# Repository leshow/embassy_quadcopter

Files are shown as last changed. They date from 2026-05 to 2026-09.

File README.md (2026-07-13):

# mini quadcopter in Rust w/ embassy for esp32 (WIP)

currently still a work in progress, building a (very) mini quadcopter for esp32 on bare metal with [embassy.dev](https://embassy.dev). right now using the esp32-c3 supermini, I may upgrade this to the s3 if the extra core is necessary.

## Quad assets

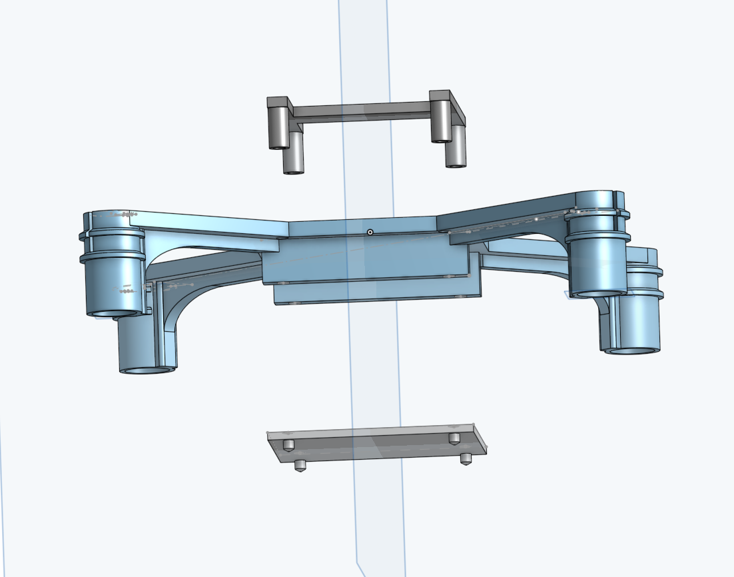
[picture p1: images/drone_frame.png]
drone frame


The frame stl & 3mf files are in the `stl/` dir and can be used to 3d print the frame. I created them in OnShape. For the battery compartment, I opted for a friction fit with pegs that you can also glue in. This got around some issues with printing supports that were a pain to remove.

There's a top stand that serves as a mount for the microcontroller and MPU6050 or ICM20948. I'll include a full parts list as the project progresses.

I've also created a prop guard you can mount as a single piece or in two halves, see the 3mf file in `stl/`

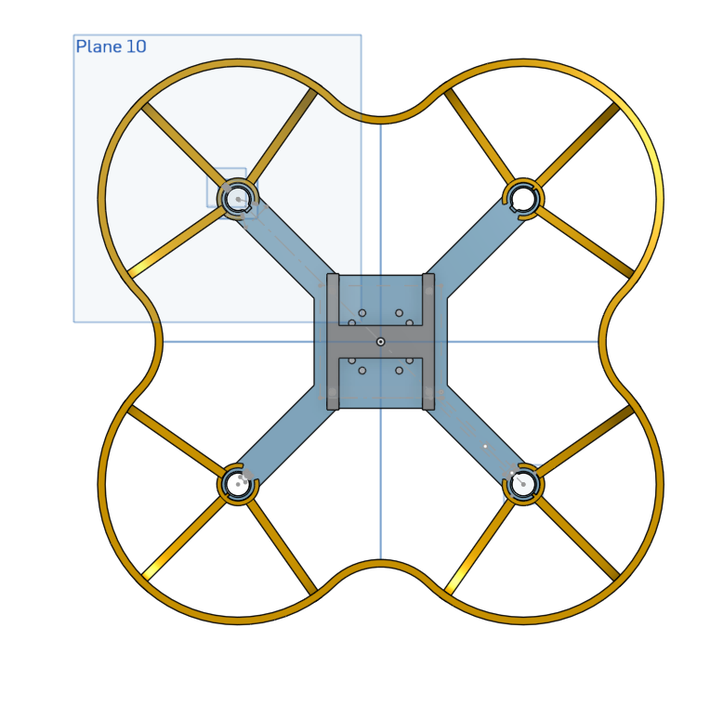
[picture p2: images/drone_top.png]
prop guard


They have a C-snap fit to the motor holders that should lock them into place pretty well. I've printed with a 0.4 and 0.6 nozzle on a bambu a1 and both results are usable. Obviously if you want cleaner layer lines go for the smaller nozzle.

I've printed in PLA, PETG and PETG-CF & GF. PLA seems totally fine, the drone frame is around 16 grams. The props are heavy at an additional 16 grams. They might require a bit of re-design but for indoor testing not so bad.

## Parts list

### Microcontrollers (choose one)

Currently only building on the c3 and c6. I'll try the s3 if I have time to attempt a build on the xtensa cores but RISC-V is better supported by embassy & Rust. The s3 supermini might be interesting because it's dual-core and has the same footprint as the c3.

| Part | Chip | Cores | Flash  | RAM | WiFi | Notes |
| --- | --- | --- | --- | --- | --- | --- |
| ESP32-C3 SuperMini | ESP32-C3 | 1× RV32 | 4 MB | 400 KB | 2.4 GHz | **Current build** - `c3` feature |
| ESP32-C6 SuperMini | ESP32-C6 | 1× RV32 | 4 MB | 512 KB | 2.4/5 GHz | Drop-in upgrade - `c6` feature |
| ESP32-S3 (16R8) | ESP32-S3 | 2× LX7  | 16 MB  | 8 MB PSRAM | 2.4 GHz | Dual-core; needs Xtensa toolchain - see `docs/s3-migration.md` |
| ESP32-S3 Mini | ESP32-S3 | 2× LX7  | 4/8 MB | - / 2 MB | 2.4 GHz | Compact form factor |

### IMU Sensors (choose)

| Part | DOF  | Interface | Accel | Gyro | Mag | Notes |
| --- | ---- | --- | ----- | ---- | --- | --- |
| ICM-20948 | 9DOF | I²C / SPI | ✓ | ✓ | ✓ AK09916 | **Current build** - yaw via magnetometer |
| MPU-6050  | 6DOF | I²C | ✓ | ✓ | ✗ | No yaw reference; cheaper and common |

### Other Components

| Part | Qty | Notes |
| --- | --- | --- |
| 8520 brushed motor | 4 | find it on aliexpress like everything else |
| mosfet 100N03A | 4 | One per motor |
| 1S LiPo battery (3.7v) | 1 | 3.7v 1s battery 25C or more discharge rate\*  |
| Propeller | 4 | 55 or 65mm |
| 3D printed frame | 1 | STL/3MF files in `stl/` - designed in OnShape |

Requires [espflash](https://github.com/esp-rs/espflash) for flashing (`cargo install espflash`).

\*I tried with a 503040 3.7v lipo recycled from a keyboard build but the BMS (battery management system) on it will automatically shut off after a few seconds. It's not really build to power these motors.

### ESP32-C3 (default)

```sh
cargo build -p embassy_quad --target riscv32imc-unknown-none-elf
cargo run -p embassy_quad --target riscv32imc-unknown-none-elf
```

Or using the aliases:

```sh
cargo build-c3
cargo flash-c3
```

### ESP32-C6

The C6 uses a different RISC-V target (`riscv32imac` vs `riscv32imc`). The
`c3` and `c6` features are mutually exclusive — always use
`--no-default-features` when building for C6 to avoid activating both:

```sh
cargo build-c6
cargo flash-c6
```

See .cargo/config.toml to see expansion of aliases

### Log level

`DEFMT_LOG` is read at compile time by `esp-println`:

```sh
DEFMT_LOG=debug cargo flash-c3
```

### Throttle cap

`THROTTLE_CAP` sets the max throttle at compile time, it will map your throttle input from 0-100 over the range you specify. For example, if you set `THROTTLE_CAP=50` and push the throttle to 80% it will translate into `.8 * 50 = 40%`.

## Visualizer

to see a 3d rendering of the orientation run:

```bash
DEFMT_LOG="info" LOG_RATE_MS=1 cargo flash-c3 --features visualize | (cd visualizer && cargo run)
```

It feeds the esp32 log output to a binary reading stdin and rendering a cube on screen

By default, sensor readings from the ICM-20948 are sent to the ESP32-C3 where either a Madgwick filter fuses accel and gyro data in software to correct orientation or the IMU's DMP is used to get the already fused output (`dmp` feature is on by default). The ICM-20948 also has an onboard DMP that fuses data directly on the sensor board. Output looks pretty good and doesn't have the yaw drift that the software fusion does when the magnetometer is enabled.

```sh
DEFMT_LOG="info" LOG_RATE_MS=1 cargo flash-c3 --features visualize | (cd visualizer && cargo run)
```

## Ground control

The `ground_control/` crate is a PC-side sender that reads a gamepad and streams control packets to the drone over UDP.

The drone runs a wifi AP (`esp-quad`, WPA2) with a static IP of `192.168.4.1`. There is no DHCP server, so you must assign yourself a static IP when connecting. The trick is to do this in a single `nmcli con add` — adding security and static IP separately doesn't work reliably:

```sh
nmcli con add type wifi con-name esp-quad ssid esp-quad \
  wifi-sec.key-mgmt wpa-psk \
  wifi-sec.psk <same as AP_PASSWORD> \
  ipv4.method manual \
  ipv4.addresses "192.168.4.2/24" \
  ipv4.gateway "192.168.4.1"
```

The AP password is set at build time via the `AP_PASSWORD` environment variable. If unset, the AP is open (remove the `wifi-sec.*` lines above).

Once the profile exists, connecting is just:

```sh
nmcli dev wifi rescan
nmcli con up esp-quad
```

Then run the ground control sender:

```sh
cd ground_control && RUST_LOG="info" cargo run --release
```

The left stick Y axis controls throttle (center = 0%, full up = 100%), left stick X controls yaw, and the right stick controls pitch/roll. The Start button toggles arm. Motors only spin when armed and throttle is above 0.

The drone IP and port can be overridden at build time:

```sh
RUST_LOG="info" GATEWAY_IP=192.168.4.1 UDP_PORT=4444 cargo run --release
```

## Testing

Unit tests live in `libs`, the crate shared between `firmware` and `ground_control` that defines the control/telemetry packet wire formats. It's the only crate that can build for the host, `firmware` can't (esp-hal's build script refuses to build for a non-embedded target), so there's nothing to run tests against there yet.

`telemetry` and `telemetry-verbose` each change the telemetry packet's wire format, so they're tested separately:

```sh
cargo test -p libs
cargo test -p libs --features telemetry
cargo test -p libs --features telemetry-verbose
```

## Docs

Check the `docs/` directory for some more info on assembly, setting up different controllers, sensors, etc.

## LLM usage

Docs and tests are sometimes generated with the use of LLMs, along with explanation/discovery, but the purpose of this project is to actually learn, so the code is still written by a human (hi!)

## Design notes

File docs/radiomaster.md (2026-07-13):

# RadioMaster Pocket as USB Gamepad for ground_control

How to configure a RadioMaster Pocket (EdgeTX) to act as a drop-in USB HID gamepad for `ground_control`, so the stick layout matches a regular Xbox-style controller with no code changes.

## Why this isn't plug and play

`ground_control` reads input through [gilrs](https://gitlab.com/gilrs-project/gilrs), which recognizes controllers by matching an SDL-style mapping database (Xbox controllers, PlayStation controllers, etc. are all in there). EdgeTX radios in USB joystick mode present a generic, fully configurable HID device under EdgeTX's own vendor ID, which is in nobody's mapping database.

Without a database entry, gilrs's Linux backend falls back to a fixed positional mapping based on the raw evdev axis/button codes (`native_ev_codes`):

| evdev code | gilrs axis/button |
| --- | --- |
| `ABS_X` | `Axis::LeftStickX`  |
| `ABS_Y` | `Axis::LeftStickY`  |
| `ABS_RX` | `Axis::RightStickX` |
| `ABS_RY` | `Axis::RightStickY` |
| `BTN_START` (0x13b) | `Button::Start` |

`ground_control` (`ground_control/src/main.rs:49-69`) maps those to controls:

- `LeftStickY` -> throttle
- `LeftStickX` -> yaw
- `RightStickX` -> roll
- `RightStickY` -> pitch
- `Button::Start` -> toggles armed

So the goal is just: configure the Pocket's USB joystick output to match this
table exactly, and gilrs/`ground_control` will treat it identically to any
other gamepad.

## Use a dedicated Model

Do this setup in its own EdgeTX Model (Model Select screen), separate from any model you bind to a real receiver over ELRS later. Mixer, Outputs, and USB Joystick settings are all per-model in EdgeTX - nothing here can leak into a flight model, but it's one less thing to think about if the USB test config and the real flight config never share a save file.

## Advanced mode may not be available on your firmware

The instructions below assume EdgeTX's "Advanced" USB Joystick mode
(free-form per-channel axis/button picker, per-axis invert, Gamepad/Joystick
toggle). The Pocket uses an STM32F407xE chip with only 512KB flash, and since
EdgeTX 2.11 the build unconditionally disables this feature (`USBJ_EX`) for
that flash size because it doesn't fit
(`radio/src/targets/taranis/CMakeLists.txt`, confirmed in
[EdgeTX/edgetx#6434](https://github.com/EdgeTX/edgetx/issues/6434)). If the
USB Joystick page only shows Classic mode with no Advanced option, you're on
2.11+ and this is why - it's not a menu you're missing.

Three ways to proceed, roughly in order of effort:

1. **Flash EdgeTX 2.10.6** - the last release with Advanced mode intact on the
   Pocket. A normal firmware flash via EdgeTX Buddy/the bootloader, no
   building required. Since this is a new model anyway there's no old-model
   storage format to migrate. Back up the SD card first as a matter of
   course. Once on 2.10.6, follow the Advanced-mode steps below as written.
1. **Stay on stock 2.11+ firmware and use Classic mode instead** - no
   firmware changes at all, but more limited (fixed channel-to-axis order, no
   per-axis invert). See "USB Joystick setup - Classic mode" further down.

## USB Joystick setup - Advanced mode

1. Press MDL, page to SETUP
1. Set USB mode to **Advanced**
1. Set **Interface Mode** to **Gamepad**, not Joystick. This matters more than
   it sounds: Linux's HID driver maps HID button usages to a totally different
   evdev range depending on this setting (`BTN_TRIGGER`-family for Joystick,
   `BTN_SOUTH..BTN_THUMBR`-family for Gamepad). gilrs's fallback mapping only
   recognizes the Gamepad range, under Joystick mode, no button will ever
   register as `Button::Start`, no matter which number you pick.
1. In Channel Settings, assign axes by **which physical stick drives the
   channel**, not by channel number (channel order depends on your model's
   template/mode and won't match this table 1:1):

   | Control                              | Axis |
   | ------------------------------------ | ---- |
   | Rudder / yaw (left stick, horiz)     | X    |
   | Throttle (left stick, vert)          | Y    |
   | Aileron / roll (right stick, horiz)  | rotX |
   | Elevator / pitch (right stick, vert) | rotY |

   Leave every other channel `None` for now.

1. Arm/disarm button: pick a spare channel, set its source to a momentary
   control (the Pocket's **SE** button is a good fit - it's momentary, not
   latching, so each press cleanly toggles arm state without a mismatch
   between switch position and armed state). Set that channel's type to
   **Btn**, button number **12** (HID button usage 12 -> evdev `BTN_START` ->
   gilrs `Button::Start`).
1. If an axis reads backwards (e.g. throttle low at stick-up), use the invert
   control inside this same USB Joystick screen (not the Mixer's channel
   weight) - it only affects how the value is packaged into the HID report,
   not the underlying channel output other things (like a real RF link) would
   read.

After any change here, disconnect and reconnect USB, you may need to power cycle the controller too.

## USB Joystick setup - Classic mode

If you're staying on stock 2.11+ firmware (option 3 above), Classic mode has
no per-channel axis picker - it maps a fixed channel order onto axes and
buttons: **channel 1->X, 2->Y, 3->Z, 4->rotX, 5->rotY, 6->rotZ, 9-32->buttons
1-24** (button N = channel N+8). There's also no per-axis invert control - use
Mixer Weight/Offset on the channel instead. Interface Mode (Gamepad vs
Joystick) isn't selectable either, but that's fine: without `USBJ_EX` it's
hardcoded to Gamepad, which is what we want anyway (confirmed in the same
issue thread - someone without `USBJ_EX` had to hand-patch firmware source to
get Joystick type instead, meaning Gamepad is the compiled-in default).

Since Classic mode just reads whatever value ends up on a given channel
number, the trick is to **use the Mixer to put the right control on the right
channel number**, rather than assigning an axis to an existing channel:

1. In Model Setup (or Outputs page), set **Number of Channels** to at least
   **20** - channel 20 is needed for the arm button below, and the default
   model channel count usually doesn't go that high.
2. Turn off the internal/external RF module for this model (recommended by
   the EdgeTX manual for USB joystick use, and irrelevant anyway since this
   model is USB-only).
3. In the Mixer, set up these channels (delete/reassign whatever the default
   template put on CH1/2/4/5 first):

   | Channel | Source                               | -> Axis (Classic order)  |
   | ------- | ------------------------------------ | ------------------------ |
   | CH1     | Rudder / yaw (left stick, horiz)     | X                        |
   | CH2     | Throttle (left stick, vert)          | Y                        |
   | CH4     | Aileron / roll (right stick, horiz)  | rotX                     |
   | CH5     | Elevator / pitch (right stick, vert) | rotY                     |
   | CH20    | **SE** button (momentary)            | button 12 -> `BTN_START` |

   Leave CH3, CH6-19 unassigned - Z/rotZ (CH3/CH6) aren't read by
   `ground_control`, and gilrs doesn't care about gaps in the button range.
   SE is used for arm/disarm because it's momentary (press+release), so it
   toggles cleanly without a switch-position/armed-state mismatch

4. If an axis reads backwards (e.g. throttle low at stick-up), fix it on the
   same Mixer line with **Weight -100%** instead of a dedicated invert
   control. Since this model is USB-only, inverting the real channel value
   here is fine - it doesn't feed a real RF link.
5. Optional: since a gamepad thumbstick springs back to center but the
   Pocket's throttle stick doesn't, you can use the _entire_ physical throttle
   throw for 0-100% instead of just the top half (which is what
   `ground_control` expects from a self-centering stick) by setting the CH2 mix to **Weight 50%,
   Offset +50** (adjust sign to taste). That compresses the full stick travel
   into the positive half of the reported axis, giving full resolution with
   no code changes. This trick works the same way regardless of Classic vs
   Advanced mode, since it's purely a Mixer-level rescale.

After any change here, disconnect and reconnect USB - you may need to power
cycle the controller too (see the USB wedge gotcha below).

## Verifying

Check the device enumerated correctly and has axes/buttons mapped right:

```sh
journalctl -k -n 100 | grep -i "radiomaster\|1209:4f54"
udevadm info -q property -n /dev/input/eventNN | grep ID_INPUT
```

You want to see `ID_INPUT_JOYSTICK=1`. If it's missing, the device has no axes/buttons configured yet.

Then run `ground_control` and watch its existing log lines while moving each stick and the arm button - `throttle:`, `roll:`, `pitch:`, `yaw:`, and `armed:` to confirm the mapping and polarity match a normal controller before flying anything.

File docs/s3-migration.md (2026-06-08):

# ESP32-S3 Migration Notes

If more compute or dual-core WiFi is needed, here is how to add S3 support
alongside the existing C3/C6 RISC-V builds.

## Why a separate subdirectory

The S3 uses an Xtensa LX7 core. Xtensa support is not in upstream Rust — it
requires Espressif's compiler fork installed via `espup`. That fork uses
`channel = "esp"` in `rust-toolchain.toml`, which does not support
`rustup target add` and cannot share a toolchain file with the stable RISC-V
builds. A subdirectory with its own `rust-toolchain.toml` is the cleanest
solution.

## Prerequisites

```sh
cargo install espup
espup install
# espup prints two exports — add them to ~/.zshrc or source before S3 builds:
export LIBCLANG_PATH="..."
export PATH="...:$PATH"
# found in ~/export-esp.sh
```

## Generating the S3 crate

From the repo root:

```sh
# For the ESP32-S3 16R8 (16MB flash, 8MB octal PSRAM)
esp-generate -c esp32s3-wroom-1-octal-psram \
  -o alloc -o wifi -o unstable-hal -o embassy -o log -o wokwi -o vscode \
  s3

# For the ESP32-S3 Mini with 2MB PSRAM
esp-generate -c esp32s3-mini-1-psram \
  -o alloc -o wifi -o unstable-hal -o embassy -o log -o wokwi -o vscode \
  s3-mini
```

Then exclude the new crate from the root workspace so the parent toolchain
does not try to build it:

```toml
# Cargo.toml (root)
[workspace]
exclude = ["s3", "s3-mini"]
```

## Porting the fusion code

The fusion module (`src/fusion.rs`) is `no_std` and has no chip-specific
dependencies — it can be shared directly.

```sh
cargo new --lib fusion-lib
```

Move `fusion.rs` content into `fusion-lib/src/lib.rs`, then reference it
from both crates:

```toml
# root Cargo.toml and s3/Cargo.toml
fusion-lib = { path = "../fusion-lib" }
```

## Key differences in main.rs for S3

- The I2C peripheral is the same `esp-hal` API — no sensor code changes.
- Two cores available via Embassy: pin the control loop task to core 0 and
  WiFi/comms to core 1 using `#[embassy_executor::task]` with core affinity.
- `esp_println` remains the same; `init_logger_from_env()` is unchanged.
- The `LOOP_PERIOD_MS` constant and fusion builder setup are identical.

## Build commands once set up

```sh
# From the s3/ subdirectory:
cd s3
cargo build
cargo run   # flash + monitor via espflash
```

The generated `.cargo/config.toml` inside `s3/` will have the correct
`xtensa-esp32s3-none-elf` target and runner already configured.

---

## Alternative: ESP-IDF (FreeRTOS) instead of bare-metal Embassy

Rather than bare-metal Embassy, the S3 can run on top of Espressif's
**ESP-IDF** SDK, which uses **FreeRTOS** as its underlying RTOS. Rust code
runs as a standard application on top of it via the `esp-idf-hal` and
`esp-idf-svc` crates.

### Generating an ESP-IDF project

```sh
cargo install cargo-generate
cargo generate --git https://github.com/esp-rs/esp-idf-template
```

The template asks for the target chip and configures the build system
(CMake + idf.py underneath, driven by `embuild` from Cargo).

### Building and flashing

```sh
cargo run --target xtensa-esp32s3-espidf
```

Note the target is `xtensa-esp32s3-espidf` (not `none-elf`) — the `espidf`
suffix means the standard library is available via ESP-IDF's newlib libc.

### Advantages over bare-metal Embassy

- **`std` is available** — `String`, `Vec`, `HashMap`, threads, sockets all
  work. Much easier to write application-level code.
- **WiFi/BLE are well supported** — `esp-idf-svc` wraps the mature ESP-IDF
  WiFi stack with a clean Rust API. Getting a TCP socket or HTTP client
  working is straightforward.
- **FreeRTOS tasks** — familiar task/thread model with priorities. Pinning
  the control loop to core 0 and WiFi to core 1 is simple.
- **Larger ecosystem** — ESP-IDF has years of production use; drivers for
  most peripherals already exist as C libraries bindable from Rust.

### Disadvantages

- **Latency and determinism** — FreeRTOS introduces scheduling jitter. The
  control loop is not guaranteed to run at exactly 200 Hz; an Embassy
  bare-metal loop is more predictable.
- **Much larger binary and RAM footprint** — ESP-IDF pulls in a full network
  stack, NVS, partition table management etc. Bare-metal Embassy fits in
  ~100 KB; an ESP-IDF build starts at ~1 MB.
- **Slower build times** — the first build compiles ESP-IDF from source via
  CMake, which takes several minutes. Incremental builds are faster but still
  slower than a pure Rust build.
- **`no_std` code needs porting** — `fusion.rs` uses `no_std` with `libm`
  for float ops. Under ESP-IDF you can keep it `no_std` or switch to `std`
  float (which is fine since `std` is available). Either works; just remove
  the `libm` calls and use `f32::atan2` etc. directly.

### Which to choose

For a **flight controller** where the PID loop timing matters: stick with
bare-metal Embassy. For a **companion computer** role (WiFi telemetry,
configuration server, OTA updates) running alongside a dedicated flight
controller: ESP-IDF is the better fit.

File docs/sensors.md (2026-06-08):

# Sensor Reference

## Axis Convention (ICM-20948 and MPU-6050)

```
        +Y (forward)
         ↑
         |
-X ------+------ +X (right)
         |
         ↓
        -Y (back)

+Z points UP out of the chip surface
-Z points DOWN into the desk
```

The physical orientation of the chip on the board determines which way these
axes point relative to the drone frame. If the chip is rotated 90°, X and Y
swap. Verify by placing the board flat and checking that `acc.z ≈ +1g`.

---

## Accelerometer (`acc.x`, `acc.y`, `acc.z`)

Measures force per unit mass in **g** (1g = 9.8 m/s²). At rest the sensor
measures gravity, which registers as a +Z force because the chip is being
pushed upward against gravity.

| Board position  | acc.x | acc.y | acc.z |
| --- | ----- | ----- | ----- |
| Flat on desk | ≈ 0 | ≈ 0 | ≈ +1g |
| Tilted right | ≈ +1g | ≈ 0 | ≈ 0 |
| Tilted left | ≈ -1g | ≈ 0 | ≈ 0 |
| Nose up (pitch) | ≈ 0 | ≈ -1g | ≈ 0 |
| Nose down | ≈ 0 | ≈ +1g | ≈ 0 |
| Upside down | ≈ 0 | ≈ 0 | ≈ -1g |

**Weakness:** Cannot distinguish tilt from linear acceleration. Under throttle
or vibration the readings are corrupted.

---

## Gyroscope (`gyro.x`, `gyro.y`, `gyro.z`)

Measures angular velocity in **rad/s** around each axis. Sign follows the
right-hand rule: curl the right hand's fingers in the direction of rotation,
thumb points along the positive axis.

| Motion | Primary axis |
| --- | --- |
| Rolling right | gyro.x > 0 |
| Rolling left | gyro.x < 0 |
| Pitching nose up | gyro.y > 0 |
| Pitching nose down | gyro.y < 0 |
| Yawing left | gyro.z > 0 |
| Yawing right | gyro.z < 0 |

**Weakness:** Integrating gyro rate over time accumulates drift. A stationary
sensor will slowly show a growing angle that isn't real.

---

## Roll and Pitch from Accelerometer

From [NXP application note AN3461](https://www.nxp.com/docs/en/application-note/AN3461.pdf),
equations 28 and 29.

$$\phi_{roll} = \text{atan2}(a_y,\ \sqrt{a_x^2 + a_z^2})$$

$$\theta_{pitch} = \text{atan2}(-a_x,\ \sqrt{a_y^2 + a_z^2})$$

`atan2` is used instead of `atan` to correctly handle all four quadrants
(full ±180° range rather than ±90°).

Yaw cannot be derived from the accelerometer — gravity is parallel to the yaw
axis so rotating flat on a table produces no change in `acc.x/y/z`.

---

## Complementary Filter

Fuses the gyro (accurate short-term, drifts long-term) with the accelerometer
(stable long-term, noisy short-term):

```
angle = α * (angle + gyro_rate * dt) + (1 - α) * accel_angle
```

`α` controls the crossover. Derived from a time constant τ (how long drift
correction takes):

$$\alpha = \frac{\tau}{\tau + dt}$$

| τ | α (at dt=5ms) | Behaviour |
| ---- | --- | --- |
| 0.1s | 0.980 | Fast correction, more accel noise  |
| 0.5s | 0.990 | Balanced |
| 2.0s | 0.9975 | Very smooth, slow drift correction |

For a drone, `α = 0.98–0.99` is typical. Motor vibration and linear
acceleration from throttle corrupt the accel signal during flight, so leaning
heavily on the gyro is preferred.

---

## Madgwick Filter

An alternative to the complementary filter. Instead of a simple weighted
average, it uses a gradient-descent step to rotate a quaternion toward the
accelerometer (and optionally magnetometer) reference each tick.

**Parameters:**

- **`beta` (β)** — how aggressively the filter corrects toward the
  accelerometer. Higher = faster correction but more sensitive to vibration.
  Lower = smoother but more gyro drift.

  | β    | Character                                  |
  | ---- | ------------------------------------------ |
  | 0.01 | Very smooth; use with clean, low-vibe data |
  | 0.1  | Good default for bench testing             |
  | 0.3+ | Fast correction; motors will add noise     |

  Start with `0.1`. Reduce if motor vibration is visible in the output.

- **`sample_period`** — the filter constructor takes an initial estimate of
  loop period in seconds. It is overwritten with the real measured `dt` on
  every update call, so the initial value is a hint only. Set it to match your
  target loop rate (e.g. `0.005` for 200 Hz).

**`dt` and the main loop timer:**

The main loop sleeps for 5 ms at the end of each tick:

```rust
Timer::after(Duration::from_millis(5)).await; // ~200 Hz
```

The actual elapsed time is measured with `Instant::now()` and passed to the
filter as `dt` in seconds. This self-corrects for I²C latency and scheduling
jitter — the filter always sees the real elapsed time regardless of what the
timer was set to.

**Yaw with Madgwick:**

- With accelerometer + gyro only (`update_imu`): yaw is integrated from the
  gyro and **will drift** over time. Fine for roll/pitch; do not rely on yaw.
- With magnetometer added (`update`): yaw is corrected against magnetic north.
  ICM-20948 supports this; MPU-6050 does not have a magnetometer.

---

## Yaw from Magnetometer (ICM-20948 only)

Raw magnetometer heading is computed as `atan2(-mag.y, mag.x)`, but this is
only valid when the board is perfectly flat. Tilting the board rotates the
magnetometer axes, projecting the field incorrectly.

**Tilt-compensated heading:**

$$\psi = \text{atan2}(m_y \cos\phi - m_z \sin\phi,\quad m_x \cos\theta + m_y \sin\theta \sin\phi + m_z \sin\theta \cos\phi)$$

where φ = roll, θ = pitch (radians from the complementary filter).

---

## Sensor Roles Summary

| Sensor | Provides | Good at | Bad at |
| --- | --- | --- | --- |
| Accelerometer | Absolute tilt (roll, pitch) | Long-term stability  | Linear accel, vibration |
| Gyroscope | Rotation rate | Fast motion tracking | Drift over time |
| Magnetometer  | Absolute heading (yaw) | Long-term yaw ref | Magnetic interference |

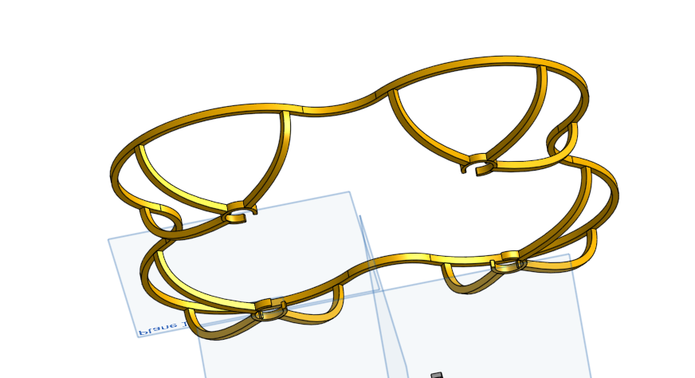
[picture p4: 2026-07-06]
images/prop_guard.png

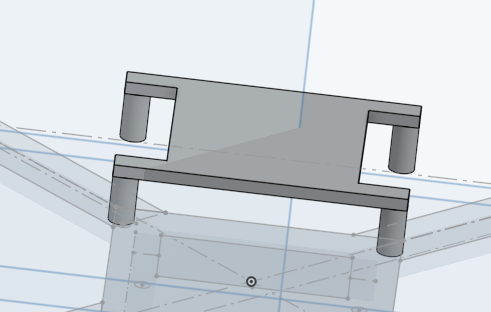
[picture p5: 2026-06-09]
images/top_stand.png

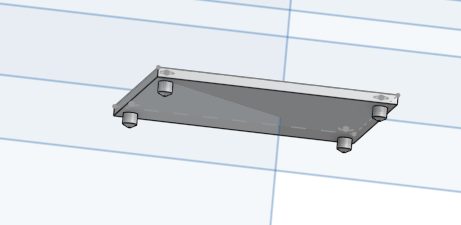
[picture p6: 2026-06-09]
images/bottom.png

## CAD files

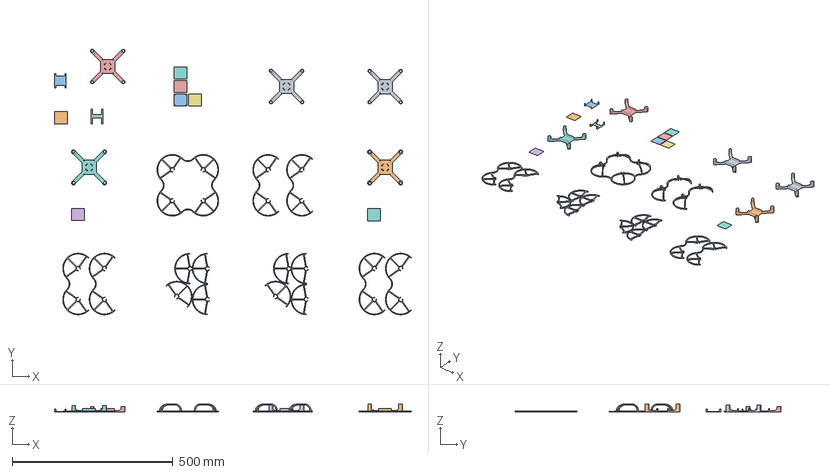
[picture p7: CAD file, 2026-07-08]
stl/PROJECT_FILE_drone.3mf
1110.5 x 826.3 x 26.0 mm
frame_20mm_tall
half guard x 2
bottom_holes
single_guard_big_tooth x 2
holes_2.2
a_big_tooth x 4
3.5mm_2.1w
3.7h_2.2w_chamfer
single guard flat b
flat guard
single guard flat a
3.7h_2.1w_chamfer x 3
flat guard x 2
frame_25mm_prop_guard
flag guard
20mmtall_prop_guard
frame_20mm_prop_guard
frame_20mm_8.7motor
top_esp32c3
frame_18mm_8.9motor

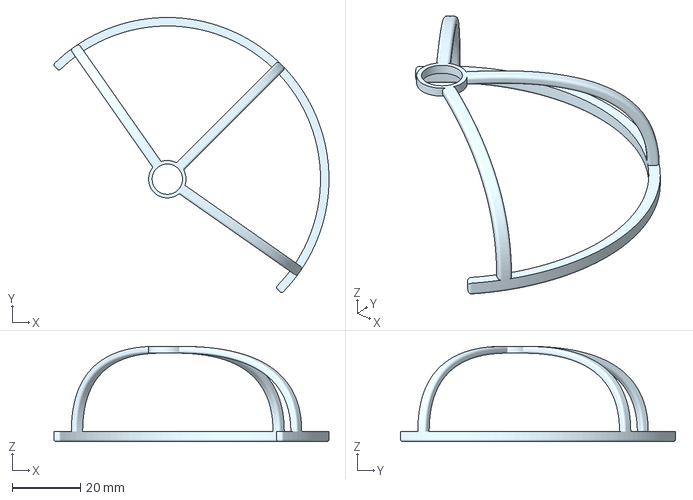
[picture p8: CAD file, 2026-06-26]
stl/fan_guard_back_right.3mf
80.8 x 80.8 x 28.0 mm

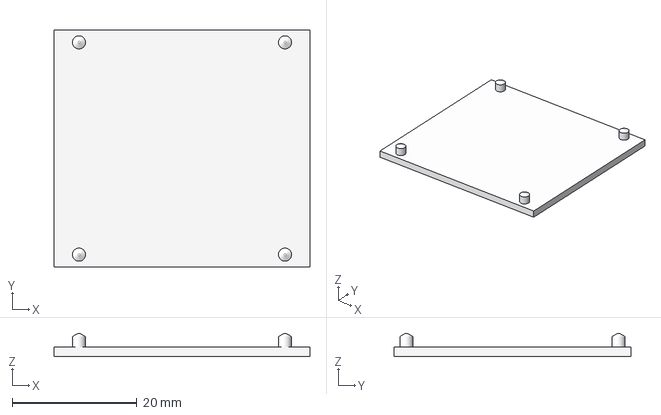
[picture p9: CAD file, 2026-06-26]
stl/battery_holder_pegs.3mf
41.0 x 38.0 x 3.70 mm

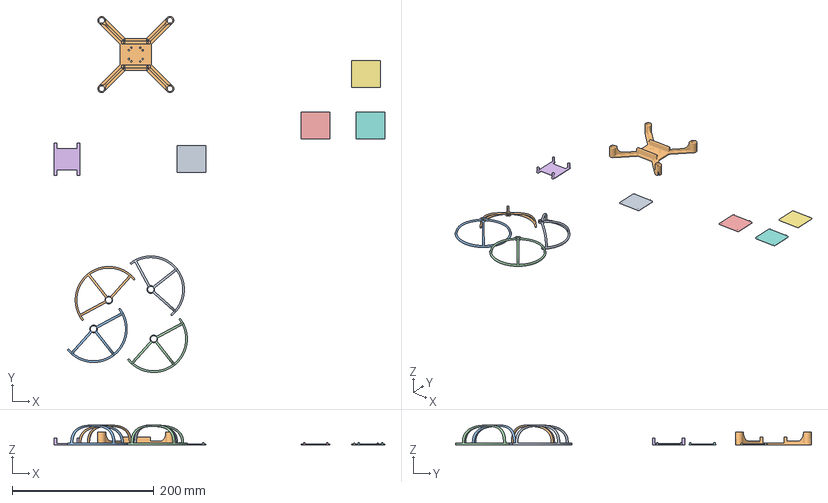
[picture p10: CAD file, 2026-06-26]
stl/PROJECT_FILE_quad.3mf
467.4 x 503.1 x 28.0 mm
FR_guard
BL_guard
BR_guard
FL_guard
3.5mm_2.1w
holes_2.2
3.7h_2.2w_chamfer
3.7h_2.1w_chamfer
frame

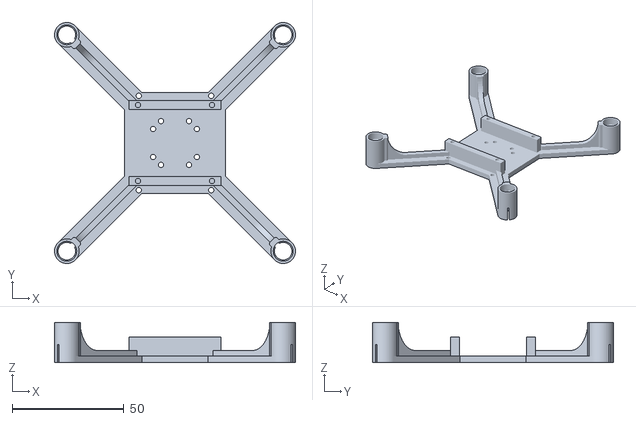
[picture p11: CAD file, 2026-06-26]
stl/frame.stl
107.6 x 107.6 x 18.0

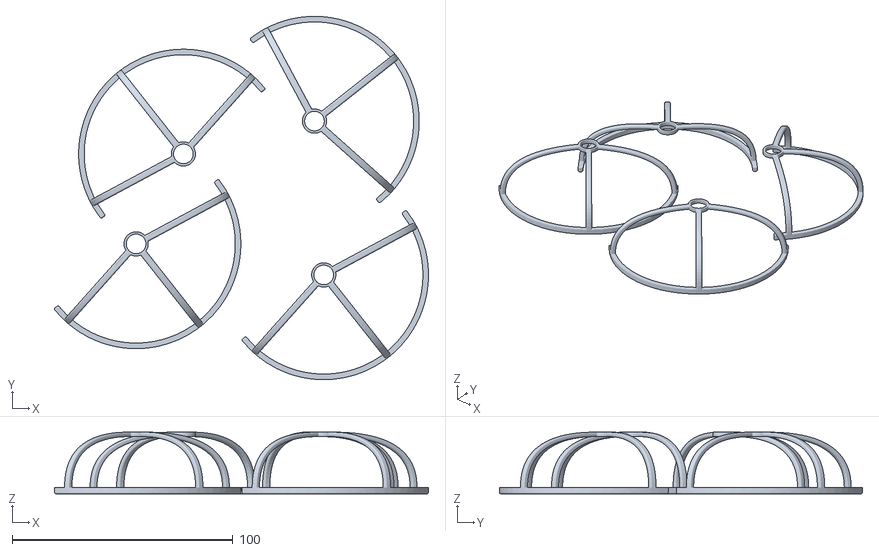
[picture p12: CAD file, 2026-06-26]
stl/fan_guards.stl
169.6 x 164.7 x 28.0

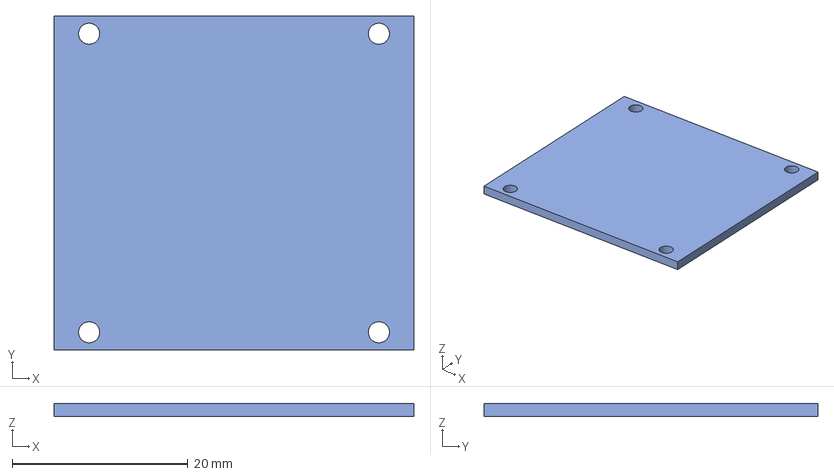
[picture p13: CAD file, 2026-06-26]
stl/battery_holder_holes.3mf
41.0 x 38.0 x 1.50 mm

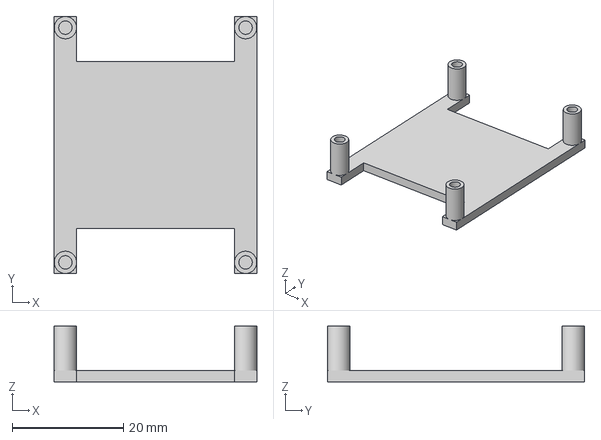
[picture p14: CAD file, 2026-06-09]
stl/top_stand.3mf
36.3 x 46.1 x 10.0 mm

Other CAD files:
stl/fan_guard_back_left.3mf
stl/fan_guard_front_left.3mf
stl/fan_guard_front_right.3mf
stl/battery_holder_holes.stl
stl/battery_holder_pegs.stl
stl/top_stand.stl

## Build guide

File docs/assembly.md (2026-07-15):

# Drone Assembly

## Parts

- ESP32-C3 SuperMini
- ICM-20948 IMU breakout
- 4× 100N03A N-channel MOSFET (one per motor)
- 4× 10kΩ resistor (gate pull-down, one per MOSFET)
- 4× 8520 brushed DC motor
- 5V boost converter
- 2× 470μF electrolytic capacitor
- 1S LiPo battery (3.7V)
- 55mm or 65mm propellers

---

## Connection Tables

### Power

| From | To | Notes |
| --- | --- | --- |
| Battery + | Boost converter IN+ | |
| Battery − | Boost converter IN− | |
| Boost converter 5V out | ESP32 VIN | 5V regulated |
| Boost converter GND | ESP32 GND | Common ground for all logic |
| 470μF cap (boost) + | Boost converter 5V out | Positive leg to 5V out |
| 470μF cap (boost) − | Boost converter GND | Prevents brownout during motor inrush |
| 470μF cap (battery) +  | Battery + | Second cap, across the battery rail |
| 470μF cap (battery) −  | Battery − | |
| Battery + | motor+ | Raw battery rail to motor switches |
| Battery − / GND | All GND lines + mosfet source | Shared ground for motors and logic |

### ICM-20948 IMU

| ICM-20948 | ESP32-C3 | Notes |
| --- | --- | --- |
| VIN | 3.3V | Regulated output from ESP32 |
| GND | GND | |
| SDA | GPIO20 | I2C data |
| SCL | GPIO21 | I2C clock (400 kHz) |
| INT | GPIO6 | Data-ready interrupt |
| CS | 3.3V | Tie HIGH to select I2C mode |
| SDO | 3.3V | Sets I2C address to 0x69 (AD0 high) |

### Motors (via 100N03A MOSFET)

| Motor | Gate (ESP32) | Gate-Source | Drain | Source |
| --- | --- | --- | --- | --- |
| Front Left  | GPIO10 | 10k pull-down | Motor − | GND |
| Front Right | GPIO9 | 10k pull-down | Motor − | GND |
| Rear Left | GPIO1 | 10k pull-down | Motor − | GND |
| Rear Right  | GPIO3 | 10k pull-down | Motor − | GND |

Motor + on all four motors connects directly to Battery +. Motor − connects to MOSFET Drain.

---

## Wiring Diagrams

### ESP32-C3 Connections

```text
          ┌───────────────────────┐
   3.3V ──┤                       ├──► ICM-20948 VIN
   3.3V ──┤                       ├──► ICM-20948 CS
   3.3V ──┤       ESP32-C3        ├──► ICM-20948 SDO
    GND ──┤                       ├──► ICM-20948 GND
          │                       │
 GPIO20 ──┤ SDA                   ├──► ICM-20948 SDA
 GPIO21 ──┤ SCL                   ├──► ICM-20948 SCL
  GPIO6 ──┤ INT                   ├──► ICM-20948 INT
          │                       │
 GPIO10 ──┤ FL PWM                ├──► MOSFET FL Gate
  GPIO9 ──┤ FR PWM                ├──► MOSFET FR Gate
  GPIO1 ──┤ RL PWM                ├──► MOSFET RL Gate
  GPIO3 ──┤ RR PWM                ├──► MOSFET RR Gate
          └───────────────────────┘
```

### Motor Layout (top-down view)

```text
                    FRONT
                      ▲
                      │
     FL (GPIO10)      │       FR (GPIO9)
         ◎────────────┼────────────◎
         │            │            │
         │       ┌────┴────┐       │
         │       │ICM20948 │       │
         │       └────┬────┘       │
         │            │            │
         ◎────────────┼────────────◎
     RL (GPIO1)       │       RR (GPIO3)
                      │
                      ▼
                     BACK
```

### MOSFET Wiring (per motor, repeated ×4)

```text
  Battery + ──────────────────────── Motor +
                                       │
                                    [Motor]
                                       │
                                    Motor − ──── Drain
                                              [100N03A]
  ESP32 GPIO ──────────── Gate         Source ──── GND
                        ┌──┘
                     [10kΩ]        pull-down holds gate low during boot/reset
                        └──┐
                          GND
```

---

## Assembly Notes

- Tie ICM-20948 CS to 3.3V — CS HIGH selects I2C mode; CS low puts the chip in SPI mode and it will not respond to I2C
- Tie ICM-20948 SDO to 3.3V — this sets the I2C address to 0x69, matching the firmware default
- The 10kΩ gate–source resistor on each MOSFET holds the gate low when the ESP32 GPIO is floating (boot/reset), preventing unintended motor spin-up
- MOSFETs are wired low-side: Drain to Motor −, Source to GND, Motor + connects directly to Battery +. N-channel MOSFETs cannot be used as high-side switches with a 3.3V gate signal
- Solder one 470μF electrolytic capacitor across the boost converter 5V output and GND, as close to those pads as possible (positive leg to 5V). This prevents the ESP32 from browning out during motor inrush current spikes
- (if using boost converter with bat +/- out) Solder the second 470μF electrolytic capacitor across Battery + and Battery −, as close to the battery leads as possible (positive leg to Battery +). This buffers the raw battery rail against motor inrush current
- All four MOSFET sources share GND; run a single wire to a bus point and branch from there
- Keep IMU signal wires (SDA/SCL/INT) routed away from motor wires to reduce noise coupling
- The ESP32 3.3V output powers the IMU; do not connect IMU VIN to the 5V boost output

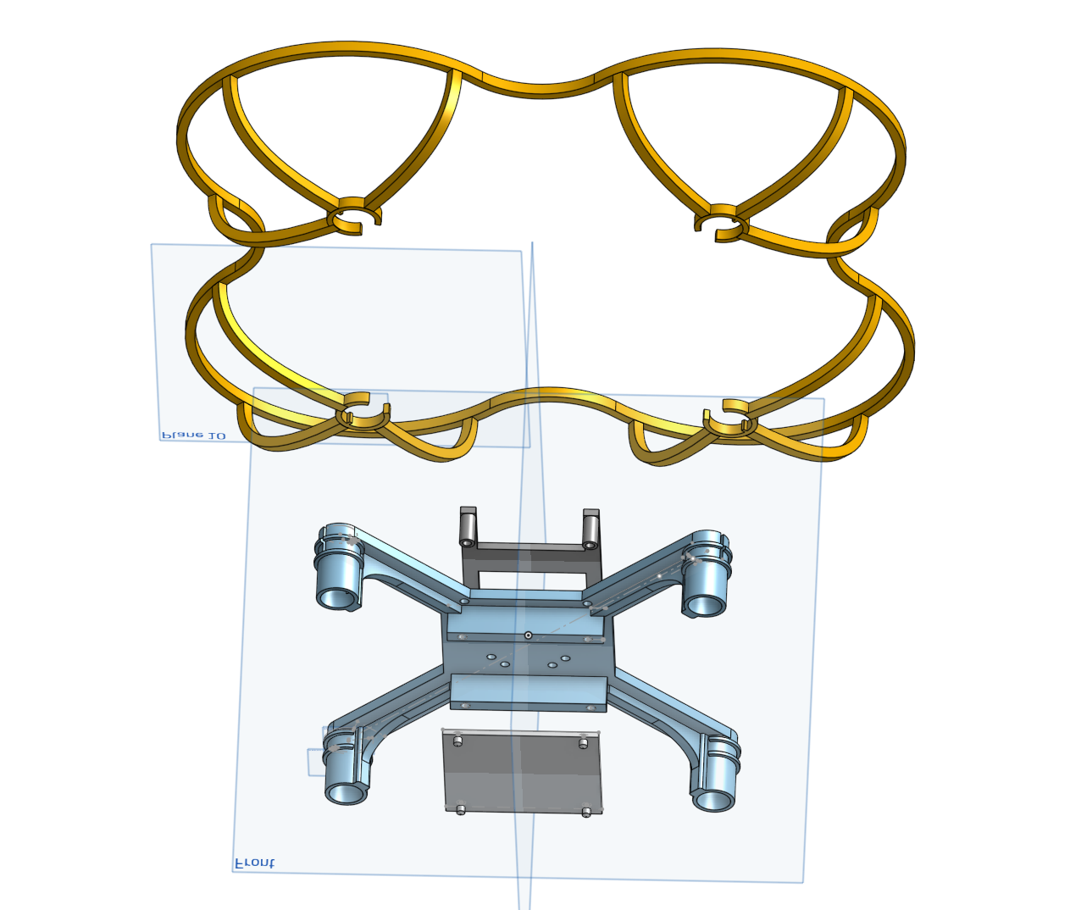
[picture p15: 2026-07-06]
images/assembly.png

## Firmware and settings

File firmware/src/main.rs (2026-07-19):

#![allow(clippy::too_many_arguments)]
#![cfg_attr(feature = "calibrate", allow(unused))]
#![no_std]
#![no_main]
extern crate alloc;

use defmt::info;
use embassy_executor::Spawner;
use embassy_time::Timer;
use esp_backtrace as _;
use esp_hal::{
    Async, gpio,
    i2c::master::{Config as I2cConfig, I2c},
    interrupt::software::SoftwareInterruptControl,
    ledc::{
        LSGlobalClkSource, Ledc, LowSpeed,
        timer::{self, TimerIFace, config::Duty},
    },
    peripherals::LEDC,
    ram,
    time::Rate,
    timer::timg::TimerGroup,
};
use esp_println as _;
use static_cell::StaticCell;

esp_bootloader_esp_idf::esp_app_desc!();

mod accel_hw_offset;
mod calibration_storage;
mod flight;
mod fusion;
mod motors;
mod panic_safety;
mod sensors;
mod wifi;

use crate::{flight::AccelBias, motors::Motors, sensors::Sensor, wifi::AP};

const LOOP_PERIOD_MS: u64 = 1; // 1000Hz target loop rate; shared by timer and Madgwick sample_period
// if changing duty cycle, change this value. currently 10 bit resolution
const PWM_BITS: u32 = 10;
const PWM_MAX_DUTY: u32 = (1 << PWM_BITS) - 1;

static TIMER: StaticCell<timer::Timer<'static, LowSpeed>> = StaticCell::new();

const fn parse_u64(s: &str) -> u64 {
    // unfortunately parse is not a const fn
    let b = s.as_bytes();
    let mut n = 0u64;
    let mut i = 0;
    // no for loops in const either? damn.
    while i < b.len() {
        n = n * 10 + (b[i] - b'0') as u64;
        i += 1;
    }
    n
}

/// How many loop iterations to skip between log lines.
/// Override at build time: `LOG_RATE_MS=200 cargo flash-c3` (default: 500 ms).
const LOG_EVERY_N: u32 = {
    let ms = match option_env!("LOG_RATE_MS") {
        Some(s) => parse_u64(s),
        None => 500,
    };
    (ms / LOOP_PERIOD_MS) as u32
};

/// cap on throttle for testing
const THROTTLE_CAP: u8 = {
    match option_env!("THROTTLE_CAP") {
        Some(s) => {
            let v = parse_u64(s);
            assert!(v <= 100, "THROTTLE_CAP must be 0..=100");
            v as u8
        }
        None => 100, // no cap default
    }
};

const fn pwm_duty_config(bits: u32) -> Duty {
    match bits {
        1 => Duty::Duty1Bit,
        2 => Duty::Duty2Bit,
        3 => Duty::Duty3Bit,
        4 => Duty::Duty4Bit,
        5 => Duty::Duty5Bit,
        6 => Duty::Duty6Bit,
        7 => Duty::Duty7Bit,
        8 => Duty::Duty8Bit,
        9 => Duty::Duty9Bit,
        10 => Duty::Duty10Bit,
        11 => Duty::Duty11Bit,
        12 => Duty::Duty12Bit,
        13 => Duty::Duty13Bit,
        14 => Duty::Duty14Bit,
        _ => panic!("failed to pick PWM duty"),
    }
}

#[esp_rtos::main]
async fn main(spawner: Spawner) {
    let peripherals = esp_hal::init(esp_hal::Config::default());

    // wifi heap only needed when running the AP, visualize mode just logs over USB
    #[cfg(not(feature = "visualize"))]
    {
        esp_alloc::heap_allocator!(#[ram(reclaimed)] size: 64 * 1024);
        esp_alloc::heap_allocator!(size: 36 * 1024);
    }

    let sw_int = SoftwareInterruptControl::new(peripherals.SW_INTERRUPT);
    let timg0 = TimerGroup::new(peripherals.TIMG0);
    esp_rtos::start(timg0.timer0, sw_int.software_interrupt0);

    #[cfg(not(feature = "visualize"))]
    let ap = AP::init(peripherals.WIFI, spawner).await;
    #[cfg(not(any(feature = "calibrate", feature = "visualize")))]
    ap.listen_control(spawner);
    #[cfg(feature = "calibrate")]
    ap.listen_calibrate(spawner);

    let i2c = I2c::new(
        peripherals.I2C0,
        I2cConfig::default().with_frequency(Rate::from_khz(400)),
    )
    .unwrap()
    .with_sda(peripherals.GPIO20)
    .with_scl(peripherals.GPIO21)
    .into_async();

    // Wait for ICM20948 to power up before init
    Timer::after_millis(500).await;

    #[cfg(not(any(feature = "calibrate", feature = "visualize")))]
    {
        let int_pin = gpio::Input::new(peripherals.GPIO6, gpio::InputConfig::default());
        run(
            i2c,
            peripherals.LEDC,
            peripherals.FLASH,
            peripherals.GPIO1,  // rear left
            peripherals.GPIO3,  // rear right
            peripherals.GPIO10, // front left
            peripherals.GPIO9,  // front right
            int_pin,
        )
        .await;
    }

    #[cfg(feature = "calibrate")]
    {
        // ICM20948
        let mut sensor = Sensor::init_icm20948(i2c)
            .await
            .expect("ICM20948 init failed");
        let accel_bias = sensor.run_calibration().await;

        let mut flash_storage = esp_storage::FlashStorage::new(peripherals.FLASH);
        let saved = calibration_storage::store_accel_calibration(&mut flash_storage, &accel_bias);
        let mode = if saved {
            defmt::info!("calibration saved: {}", defmt::Debug2Format(&accel_bias));
            libs::calibrate::CalibrationMode::Ended
        } else {
            defmt::error!("failed to save calibration to flash");
            libs::calibrate::CalibrationMode::Failed
        };
        wifi::calibrate::EVENTS
            .publisher()
            .expect("calibration publisher already taken")
            .publish(mode)
            .await;
    }

    #[cfg(feature = "visualize")]
    {
        let int_pin = gpio::Input::new(peripherals.GPIO6, gpio::InputConfig::default());
        run_visualizer(i2c, peripherals.FLASH, int_pin).await;
    }
}

async fn run(
    i2c: I2c<'_, esp_hal::Async>,
    ledc: LEDC<'static>,
    flash: esp_hal::peripherals::FLASH<'static>,
    rear_left_pin: impl gpio::interconnect::PeripheralOutput<'static>,
    rear_right_pin: impl gpio::interconnect::PeripheralOutput<'static>,
    front_left_pin: impl gpio::interconnect::PeripheralOutput<'static>,
    front_right_pin: impl gpio::interconnect::PeripheralOutput<'static>,
    int_pin: gpio::Input<'static>,
) {
    let mut ledc = Ledc::new(ledc);
    ledc.set_global_slow_clock(LSGlobalClkSource::APBClk);

    // Promote the configured timer to static
    let mut timer = ledc.timer::<LowSpeed>(timer::Number::Timer0);
    timer
        .configure(timer::config::Config {
            duty: pwm_duty_config(PWM_BITS),
            clock_source: timer::LSClockSource::APBClk,
            frequency: Rate::from_khz(78),
        })
        .expect("timer init failed");

    let timer_static = TIMER.init(timer);
    let motors = Motors::init_pwm(
        &ledc,
        timer_static,
        0,
        rear_left_pin,
        rear_right_pin,
        front_left_pin,
        front_right_pin,
    )
    .await;
    // ICM20948
    // gyro bias is tracked continuously in flight::run_control
    let sensor = match Sensor::init_icm20948(i2c).await {
        Ok(s) => s,
        Err(e) => {
            defmt::error!("ICM20948 init failed: {}", defmt::Debug2Format(&e));
            panic!("ICM20948 init failed");
        }
    };

    // accel bias/scale from the last `--features calibrate` run, if any - see
    // calibration_storage and flight::AccelBias
    let mut flash_storage = esp_storage::FlashStorage::new(flash);
    let accel_bias = calibration_storage::load_accel_calibration(&mut flash_storage)
        .inspect(|a| {
            info!("accel loaded from bias {}", defmt::Debug2Format(a));
        })
        .unwrap_or_else(|| {
            info!("no accel found, run calibration");
            AccelBias::default()
        });
    flight::run_control(sensor, int_pin, motors, accel_bias).await;
}

pub(crate) type Sensor20948<'a> =
    Sensor<icm20948::Icm20948Driver<icm20948::I2cInterface<I2c<'a, Async>>>>;

#[cfg(feature = "visualize")]
async fn run_visualizer(
    i2c: I2c<'_, esp_hal::Async>,
    #[cfg_attr(feature = "dmp", allow(unused))] flash: esp_hal::peripherals::FLASH<'static>,
    int_pin: gpio::Input<'static>,
) {
    let sensor = Sensor::init_icm20948(i2c)
        .await
        .expect("ICM20948 init failed");

    #[cfg(feature = "dmp")]
    flight::run_dmp_visualizer(sensor, int_pin).await;
    #[cfg(not(feature = "dmp"))]
    {
        let mut flash_storage = esp_storage::FlashStorage::new(flash);
        let accel_bias =
            calibration_storage::load_accel_calibration(&mut flash_storage).unwrap_or_default();
        flight::run_fusion_visualizer(sensor, int_pin, accel_bias).await;
    }
}

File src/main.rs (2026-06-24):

#![allow(clippy::too_many_arguments)]
#![cfg_attr(feature = "calibrate", allow(unused))]
#![no_std]
#![no_main]

use embassy_executor::Spawner;
use embassy_time::{Duration, Timer};
use esp_backtrace as _;
use esp_hal::{
    Async, gpio,
    i2c::master::{Config as I2cConfig, I2c},
    interrupt::software::SoftwareInterruptControl,
    ledc::{
        LSGlobalClkSource, Ledc, LowSpeed,
        channel::{self, ChannelIFace},
        timer::{self, TimerIFace},
    },
    peripherals::LEDC,
    time::Rate,
    timer::timg::TimerGroup,
};
use esp_println as _;

esp_bootloader_esp_idf::esp_app_desc!();

mod fusion;
mod sensors;

use crate::sensors::Sensor;
#[cfg(not(feature = "dmp"))]
use crate::{
    fusion::FusionBuilder,
    sensors::{ImuRead, ImuReadMag},
};

const LOOP_PERIOD_MS: u64 = 1; // 1000Hz target loop rate; shared by timer and Madgwick sample_period

/// How many loop iterations to skip between log lines.
/// Override at build time: `LOG_RATE_MS=200 cargo flash-c3` (default: 500 ms).
const LOG_EVERY_N: u32 = {
    const fn parse_u64(s: &str) -> u64 {
        // unfortunately parse is not a const fn
        let b = s.as_bytes();
        let mut n = 0u64;
        let mut i = 0;
        // no for loops in const either? damn.
        while i < b.len() {
            n = n * 10 + (b[i] - b'0') as u64;
            i += 1;
        }
        n
    }
    let ms = match option_env!("LOG_RATE_MS") {
        Some(s) => parse_u64(s),
        None => 500,
    };
    (ms / LOOP_PERIOD_MS) as u32
};

#[esp_rtos::main]
async fn main(_spawner: Spawner) {
    let peripherals = esp_hal::init(esp_hal::Config::default());

    let sw_int = SoftwareInterruptControl::new(peripherals.SW_INTERRUPT);
    let timg0 = TimerGroup::new(peripherals.TIMG0);
    esp_rtos::start(timg0.timer0, sw_int.software_interrupt0);

    // #[cfg(not(feature = "calibrate"))]
    // let (led_fwd_pitch, led_bwd_pitch, led_fwd_roll, led_bwd_roll) = (
    //     gpio::Output::new(
    //         peripherals.GPIO10,
    //         gpio::Level::Low,
    //         esp_hal::gpio::OutputConfig::default(),
    //     ),
    //     gpio::Output::new(
    //         peripherals.GPIO9,
    //         gpio::Level::Low,
    //         esp_hal::gpio::OutputConfig::default(),
    //     ),
    //     gpio::Output::new(
    //         peripherals.GPIO0,
    //         gpio::Level::Low,
    //         esp_hal::gpio::OutputConfig::default(),
    //     ),
    //     gpio::Output::new(
    //         peripherals.GPIO1,
    //         gpio::Level::Low,
    //         esp_hal::gpio::OutputConfig::default(),
    //     ),
    // );

    let i2c = I2c::new(
        peripherals.I2C0,
        I2cConfig::default().with_frequency(Rate::from_khz(400)),
    )
    .unwrap()
    .with_sda(peripherals.GPIO20)
    .with_scl(peripherals.GPIO21)
    .into_async();

    // Wait for ICM20948 to power up before init
    Timer::after(Duration::from_millis(100)).await;

    #[cfg(not(any(feature = "calibrate", feature = "visualize")))]
    {
        let int_pin = gpio::Input::new(peripherals.GPIO6, gpio::InputConfig::default());
        run(
            i2c,
            peripherals.LEDC,
            peripherals.GPIO9,
            peripherals.GPIO10,
            peripherals.GPIO0,
            peripherals.GPIO1,
            int_pin,
        )
        .await;
    }

    #[cfg(feature = "calibrate")]
    {
        // ICM20948
        let mut sensor = Sensor::init_icm20948(i2c, LOOP_PERIOD_MS)
            .await
            .expect("ICM20948 init failed");
        sensor.run_calibration().await;
    }

    #[cfg(feature = "visualize")]
    {
        let int_pin = gpio::Input::new(peripherals.GPIO6, gpio::InputConfig::default());
        run_visualizer(i2c, int_pin).await;
    }
}

async fn run(
    i2c: I2c<'_, esp_hal::Async>,
    ledc: LEDC<'static>,
    rear_left_pin: impl gpio::interconnect::PeripheralOutput<'static>,
    rear_right_pin: impl gpio::interconnect::PeripheralOutput<'static>,
    front_left_pin: impl gpio::interconnect::PeripheralOutput<'static>,
    front_right_pin: impl gpio::interconnect::PeripheralOutput<'static>,
    int_pin: gpio::Input<'static>,
) {
    let mut ledc = Ledc::new(ledc);
    ledc.set_global_slow_clock(LSGlobalClkSource::APBClk);

    let mut lstimer0 = ledc.timer::<LowSpeed>(timer::Number::Timer0);
    lstimer0
        .configure(timer::config::Config {
            duty: timer::config::Duty::Duty10Bit,
            clock_source: timer::LSClockSource::APBClk,
            frequency: Rate::from_khz(78),
        })
        .expect("timer init failed");

    let mut channel0 = ledc.channel(channel::Number::Channel0, rear_left_pin);
    channel0
        .configure(channel::config::Config {
            timer: &lstimer0,
            duty_pct: 20,
            drive_mode: esp_hal::gpio::DriveMode::PushPull,
        })
        .expect("rear left motor pwm init failed");

    let mut channel1 = ledc.channel(channel::Number::Channel1, rear_right_pin);
    channel1
        .configure(channel::config::Config {
            timer: &lstimer0,
            duty_pct: 20,
            drive_mode: esp_hal::gpio::DriveMode::PushPull,
        })
        .expect("rear right motor pwm init failed");

    let mut channel2 = ledc.channel(channel::Number::Channel2, front_left_pin);
    channel2
        .configure(channel::config::Config {
            timer: &lstimer0,
            duty_pct: 20,
            drive_mode: esp_hal::gpio::DriveMode::PushPull,
        })
        .expect("front left motor pwm init failed");

    let mut channel3 = ledc.channel(channel::Number::Channel3, front_right_pin);
    channel3
        .configure(channel::config::Config {
            timer: &lstimer0,
            duty_pct: 20,
            drive_mode: esp_hal::gpio::DriveMode::PushPull,
        })
        .expect("front right motor pwm init failed");

    defmt::info!("motors initialized: all channels 10%");

    // ICM20948
    let sensor = Sensor::init_icm20948(i2c, LOOP_PERIOD_MS)
        .await
        .expect("ICM20948 init failed");

    #[cfg(not(feature = "dmp"))]
    {
        let _ = int_pin;
        software_loop(sensor).await;
    }
    #[cfg(feature = "dmp")]
    run_dmp(sensor, int_pin).await;
}

type Sensor20948<'a> = Sensor<icm20948::Icm20948Driver<icm20948::I2cInterface<I2c<'a, Async>>>>;
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

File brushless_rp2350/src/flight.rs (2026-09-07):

use crate::{CtrlRx, motors::Motors};
use defmt::{debug, error, info};
use embassy_rp::{
    Peri,
    gpio::{Input, Pull},
    peripherals::PIN_6,
};
use embassy_time::{Duration, Instant};

use {defmt_rtt as _, panic_probe as _};

use libs::flight::{
    filters,
    fusion::{FusionBuilder, RAD_TO_DEG},
    pid::Pid,
    sensors::ImuRead,
};
use nalgebra::Vector3;

mod vals {
    use libs::flight::{filters, fusion};

    // icm426xx scales raw counts by STD_GRAVITY internally, so Sensor::read hands back m/s^2, not
    // g like the esp32-s3's driver does.
    const ONE_G: f32 = 9.80665;
    pub const ACCEL_MIN: f32 = filters::ACCEL_HEALTHY_MIN * ONE_G;
    pub const ACCEL_MAX: f32 = filters::ACCEL_HEALTHY_MAX * ONE_G;

    // scales max tilt between 0 to MAX_TILT_RAD
    pub const MAX_TILT_RAD: f32 = 45.0 * fusion::DEG_TO_RAD;

    // outer loop p gains
    pub const ANGLE_P_ROLL_PITCH: f32 = 3.0;
    // and angle_p_yaw means the controller will eventually torque
    // quad to chase drift
    pub const ANGLE_P_YAW: f32 = 0.0;

    // inner loop - only P is live for the first test. D and I come in one at a time, in that
    // order, once the previous term is confirmed stable. INTEGRAL_LIMIT/LEAK below stay
    // inert while their Ki is 0 - both only ever shape the accumulator's value, and Ki=0
    // zeroes that value's contribution to the output regardless
    pub const RATE_KP_ROLL_PITCH: f32 = 0.05;
    pub const RATE_KI_ROLL_PITCH: f32 = 0.0; // was 0.3
    pub const RATE_KD_ROLL_PITCH: f32 = 0.0; // was 0.001

    pub const RATE_KP_YAW: f32 = 0.1; // flix 0.3 was set to 0.2
    pub const RATE_KI_YAW: f32 = 0.0; // was 0.05
    pub const RATE_KD_YAW: f32 = 0.0; // was 0.001

    pub const INTEGRAL_LIMIT: f32 = 0.3;
    // per-second decay on the rate pids' integral term - without this, any permanent small error
    // eventually winds the integral to integral_limit given enough time, no matter how small the error is. with
    // decay, a persistent error settles at an equilibrium of error/rate_integral_leak instead,
    // while a genuinely larger disturbance still gets proportionally more integral authority
    pub const RATE_INTEGRAL_LEAK: f32 = 1.0;

    // outer loop angle error deadband - a resting tilt under this is mounting tolerance subtracts the band rather than clamping to it, so there's
    // no discontinuity in commanded rate right at the edge. roll/pitch only: yaw can't wind up
    // (rate_ki_yaw = 0) and has its own heading-hold handling already
    pub const ANGLE_DEADBAND_RAD: f32 = 0.5 * fusion::DEG_TO_RAD;
}

mod util {

    pub(crate) fn deadband(x: f32, band: f32) -> f32 {
        if x > band {
            x - band
        } else if x < -band {
            x + band
        } else {
            0.0
        }
    }

    /// normalises an angle to [-pi, pi] for the shortest-path
    pub(crate) fn wrap_angle(a: f32) -> f32 {
        use core::f32::consts::PI;
        // fmodf gives the same sign as the dividend, so shift into [0, 2pi) before subtracting back
        let r = libm::fmodf(a + PI, 2.0 * PI);
        (if r < 0.0 { r + 2.0 * PI } else { r }) - PI
    }

    /// running min/max/avg of loop dt between periodic log lines - lets the actual loop rate be
    /// checked without needing per-tick logging
    pub struct DtStats {
        pub min: f32,
        pub max: f32,
        pub sum: f32,
        pub n: u32,
    }

    impl DtStats {
        pub const fn new() -> Self {
            Self {
                min: f32::MAX,
                max: 0.0,
                sum: 0.0,
                n: 0,
            }
        }

        pub fn record(&mut self, dt: f32) {
            self.min = self.min.min(dt);
            self.max = self.max.max(dt);
            self.sum += dt;
            self.n += 1;
        }

        pub fn avg(&self) -> f32 {
            self.sum / self.n as f32
        }
    }
}

pub async fn run<'a, D>(
    mut sensor: crate::imu::Sensor<icm426xx::ICM42688<D, icm426xx::Ready>>,
    mut motors: Motors<'a>,
    int1: Peri<'static, PIN_6>,
    mut rx: CtrlRx<'a>,
) where
    D: embedded_hal_async::spi::SpiDevice,
    D::Error: defmt::Format,
{
    let mut log_count: u32 = 0;
    let mut int1 = Input::new(int1, Pull::None);
    let mut fusion = FusionBuilder::new().icm42688().madgwick().build();
    let mut last = Instant::now();
    let mut dt_stats = util::DtStats::new();
    let mut accel_filter = filters::Lpf3::new_two_pole(filters::ACCEL_LPF_HZ);
    // TODO: delete me
    // norm of every accel sample over a log window, plus how many the health gate threw out.
    // this is the measurement that says whether vibration is actually reaching the estimator
    let mut accel_stats = util::DtStats::new();
    let mut accel_rejects: u32 = 0;

    // inner rate PIDs
    let mut roll_pid = Pid::new(
        vals::RATE_KP_ROLL_PITCH,
        vals::RATE_KI_ROLL_PITCH,
        vals::RATE_KD_ROLL_PITCH,
        vals::INTEGRAL_LIMIT,
        vals::RATE_INTEGRAL_LEAK,
    );
    let mut pitch_pid = Pid::new(
        vals::RATE_KP_ROLL_PITCH,
        vals::RATE_KI_ROLL_PITCH,
        vals::RATE_KD_ROLL_PITCH,
        vals::INTEGRAL_LIMIT,
        vals::RATE_INTEGRAL_LEAK,
    );
    let mut yaw_pid = Pid::new(
        vals::RATE_KP_YAW,
        vals::RATE_KI_YAW,
        vals::RATE_KD_YAW,
        vals::INTEGRAL_LIMIT,
        vals::RATE_INTEGRAL_LEAK,
    );

    let mut target_yaw: f32 = 0.0;
    let mut yaw_init = false;
    let mut last_armed = false;

    loop {
        int1.wait_for_high().await;

        // gyro still goes in raw - no LPF or bias tracking on it yet unlike esp32s3
        let (accel, gyro) = match sensor.read().await {
            Ok(sample) => sample,
            Err(e) => {
                error!("ICM42688 read_sample failed: {}", e);
                continue;
            }
        };

        let now = Instant::now();
        let dt = now.duration_since(last).as_micros() as f32 / 1_000_000.0;
        last = now;
        dt_stats.record(dt);

        // the chip's anti-alias filter is set to 1/2 the imu ODR (currently 1khz)
        // everything below that arrives unfiltered
        // madgwick uses accel as its gravity reference, so a corrupted sample tilts the estimate
        // and the angle loop below then chases it with real motor output
        let accel = accel_filter.update(accel, dt);

        // outside this band the reading isn't gravity, it's vibration or motion, so its direction
        // can't be trusted as "down" no matter how smooth it is. feeding zeros makes madgwick
        // treat it as "no accel this tick" and coast on gyro integration instead of being pulled
        // by a bad reference
        let accel = if (vals::ACCEL_MIN..=vals::ACCEL_MAX).contains(&{
            let accel_norm = accel.norm();
            accel_stats.record(accel_norm);
            accel_norm
        }) {
            accel
        } else {
            accel_rejects += 1;
            Vector3::zeros()
        };
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

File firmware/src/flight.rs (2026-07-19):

use embassy_time::{Duration, Instant};
use esp_hal::gpio;
#[cfg(feature = "telemetry")]
use libs::telemetry::TelemetryPacket;
#[cfg(feature = "dmp")]
use nalgebra::Quaternion;
use nalgebra::{UnitQuaternion, Vector3};

use crate::{Motors, Sensor20948, fusion, wifi};
#[cfg(feature = "dmp")]
use crate::{fusion::MargFusion, sensors::ImuReadMag};
#[cfg(not(feature = "dmp"))]
use crate::{
    fusion::{ImuFusion, MargFusion},
    sensors::{ImuRead, ImuReadMag},
};

// publishes a telemetry snapshot for the wifi udp_task to reply with on the next control packet.
// called once per loop iteration, from whichever exit point (early continue or full mix) is
// actually taken, so telemetry is only ever built once per tick.
#[cfg(feature = "telemetry")]
#[allow(clippy::too_many_arguments)]
async fn publish_telemetry(
    euler: (f32, f32, f32),       // (roll, pitch, yaw) radians
    motors: (u16, u16, u16, u16), // fl fr rl rr
    armed: bool,
    failsafe: bool,
    gyro: Vector3<f32>,
) {
    let roll_deg = euler.0 * fusion::RAD_TO_DEG;
    let pitch_deg = euler.1 * fusion::RAD_TO_DEG;
    let yaw_deg = euler.2 * fusion::RAD_TO_DEG;

    #[cfg(not(feature = "telemetry-verbose"))]
    let _ = &gyro;

    #[cfg(not(feature = "telemetry-verbose"))]
    let pkt = TelemetryPacket::new(roll_deg, pitch_deg, yaw_deg, motors, armed, failsafe);
    #[cfg(feature = "telemetry-verbose")]
    let pkt = TelemetryPacket::new(roll_deg, pitch_deg, yaw_deg, motors, armed, failsafe, gyro);

    *wifi::TELEMETRY.lock().await = Some((pkt, Instant::now()));
}

// calibrated_gyro is i16 at +/-2000 dps full scale, hardware DLPF at 51 Hz already applied
#[cfg(feature = "dmp")]
const GYRO_SCALE: f32 = 2000.0 * fusion::DEG_TO_RAD / 32768.0; // i16 → rad/s

// max roll/pitch command from stick (+/- 25 deg)
const MAX_TILT_RAD: f32 = 25.0 * fusion::DEG_TO_RAD;

// outer loop P gains
const ANGLE_P_ROLL_PITCH: f32 = 6.0; // flix 6.0
const ANGLE_P_YAW: f32 = 2.0; // flix 3.0

// inner loop
const RATE_KP_ROLL_PITCH: f32 = 0.05; // flix 0.05
const RATE_KI_ROLL_PITCH: f32 = 0.1; // flix 0.2
const RATE_KD_ROLL_PITCH: f32 = 0.001; // flix 0.001

const RATE_KP_YAW: f32 = 0.2; // flix 0.3
const RATE_KI_YAW: f32 = 0.0;
const RATE_KD_YAW: f32 = 0.0;

// max angle any single DMP sample can plausibly rotate by since the last accepted sample
#[cfg(feature = "dmp")]
const MAX_QUAT_JUMP_RAD: f32 = 60.0 * fusion::DEG_TO_RAD;

/// PID
///
/// Proportional-Integral-Derivative controller — computes a corrective output
/// from three components of the error signal:
///
/// P proportional: output -> current error (instant response, but can oscillate)
/// I integral:     output -> accumulated past error (eliminates steady-state offset)
/// D derivative:   output -> rate of change of error (damps oscillation)
///
/// Combined: output = kp·e + ki·∫e·dt + kd·(de/dt)
struct Pid {
    /// proportional gain — how hard to push per unit of current error
    kp: f32,
    /// integral gain — how hard to push per unit of accumulated error
    ki: f32,
    /// derivative gain — how hard to damp per unit of error rate
    kd: f32,
    /// running sum of error×dt, clamped to ±integral_limit
    integral: f32,
    /// error from last tick for de/dt; NaN until first update to avoid derivative spike on arm
    prev_error: f32,
    /// anti-windup clamp — keeps integral from growing unbounded
    integral_limit: f32,
}

impl Pid {
    const fn new(kp: f32, ki: f32, kd: f32, integral_limit: f32) -> Self {
        Self {
            kp,
            ki,
            kd,
            integral: 0.0,
            prev_error: f32::NAN,
            integral_limit,
        }
    }

    fn update(&mut self, error: f32, dt: f32) -> f32 {
        // matches flix: reset if dt is zero or impossibly large
        if dt <= 0.0 || dt > 0.5 {
            self.reset();
            return self.kp * error;
        }
        self.integral =
            (self.integral + error * dt).clamp(-self.integral_limit, self.integral_limit);
        // no software LPF on derivative — hardware DLPF at 51 Hz handles it
        let derivative = if self.prev_error.is_nan() {
            0.0
        } else {
            (error - self.prev_error) / dt
        };
        self.prev_error = error;
        self.kp * error + self.ki * self.integral + self.kd * derivative
    }

    fn reset(&mut self) {
        self.integral = 0.0;
        self.prev_error = f32::NAN;
    }
}

/// AccelBias
///
/// One-time accelerometer bias + scale correction, computed by the 6-orientation tumble
/// calibration (behind `--features calibrate`) and loaded from flash at boot - see
/// `calibration_storage`. Unlike gyro bias this isn't re-learned continuously; accel bias
/// mostly comes from IMU mounting tilt and silicon offset, both fixed for a given build.
#[derive(Clone, Copy, Debug)]
#[cfg_attr(feature = "dmp", allow(dead_code))] // only applied on the non-dmp (software fusion) path
pub struct AccelBias {
    pub bias: Vector3<f32>,
    pub scale: Vector3<f32>,
}

impl Default for AccelBias {
    fn default() -> Self {
        Self {
            bias: Vector3::zeros(),
            scale: Vector3::new(1.0, 1.0, 1.0),
        }
    }
}

#[cfg_attr(feature = "dmp", allow(dead_code))]
impl AccelBias {
    // matches flix's apply step exactly: acc = (acc - accBias) / accScale
    fn apply(&self, accel: Vector3<f32>) -> Vector3<f32> {
        (accel - self.bias).component_div(&self.scale)
    }
}
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

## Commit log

2026-05-29 working i2c async
2026-05-30 four leds indicating pitch/roll
2026-06-08 add build for esp32c6
2026-06-08 refactor to Sensor supporting both mpu6050 & icm20948
2026-06-09 add model + image assets
    [PROJECT_FILE_embassy_drone.3mf, bottom_with_peg.stl, bottom_with_pegs.3mf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]
2026-06-10 Fix frame file description and motor type in README
    Corrected the description of the frame files and updated motor type in the parts list.
2026-06-10 adds vqf+mahony, swaps to use uf-ahrs library
    [main.rs]
2026-06-12 add calibration mode
    [mag_data.csv]
2026-06-13 use defmt instead of println
    [mag_data.csv]
2026-06-13 add accel+gyro config
2026-06-15 one spinning motor now
2026-06-16 add more motors
2026-06-16 spin all motors at 20%
2026-06-16 add note about battery
2026-06-23 increase i2c speed
2026-06-26 update stls and start AP+udp listener
    [PROJECT_FILE_embassy_drone.3mf, PROJECT_FILE_quad.3mf, battery_holder_holes.3mf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]
2026-06-27 test WIFI AP, add test motor spin up
